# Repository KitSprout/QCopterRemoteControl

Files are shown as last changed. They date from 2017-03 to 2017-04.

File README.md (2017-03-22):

QCopterRC
========





QCopterRemoteControl 是一個遙控器開板，四軸飛行器的控制裝置，用來與 QCopterFlightControl 溝通、控制，板上搭載搖桿與感測器，並外接顯示螢幕，可以將四軸上的回傳回來的資訊顯示出來，螢幕建立了簡單的操作介面，方便使用者設定、觀察飛控板，目前遙控器有 QCopterRC 與 QCopterRCs 兩種版本，前者使用芯片效能較高、功能多，帶高解析度的螢幕，後者功能較為簡潔，製作成本比較低。目前開發著重於 QCopterRCs，想了解 QCopterRC 的可以進入該分支 [branche](https://github.com/KitSprout/QCopterRemoteControl/tree/QCopterRC)

Hardware
========
* 控制器　 : [STM32F411CE](http://www.st.com/en/microcontrollers/stm32f411ce.html) 48Pin 100MHz DSP FPU
* 顯示器　 : [OLED_1.5-inch](https://github.com/KitSprout/OLED_1.5-inch) ( SSD1351 1.5" 128*128 )，使用 SPI 操作
* 感測器　 : [MPU9250](https://www.invensense.com/products/motion-tracking/9-axis/mpu-9250/)
* 無線傳輸 : [nRF24L01P](http://www.nordicsemi.com/eng/Products/2.4GHz-RF/nRF24L01P) + PA + LNA
* 設計軟體 [Altium Designer 17](http://www.altium.com/en/products/altium-designer) ( PcbLib use AD [PcbLib v2.16](https://github.com/KitSprout/AltiumDesigner_PcbLibrary/releases/tag/v2.16) )

View
========


<br />
[more photo...](https://goo.gl/photos/wA4TmWAdz5D3ZGH7A)

Config
========


Schematic
========


Get it
========
Ruten Shop

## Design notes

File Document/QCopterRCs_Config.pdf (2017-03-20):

PORT | AF0 SYS | AF1 TIM1 TIM2 | AF2 TIM3 TIM4 TIM5 | AF3 TIM9 TIM10 TIM11 | AF4 I2C1 I2C2 I2C3 | AF5 SPI1 SPI2 SPI4 | AF6 SPI3 SPI4 SPI5 | AF7 SPI3 USART1 USART2 | AF8 USART6 | AF9 I2C2 I2C3 | AF10 OTG_FS | AF12 SDIO | ADC | 配置

PA

PB

PC

0 | CH1 / ETR | CH1 | CTS | ADC1_IN0 | X | AD_JSL1
1 | CH2 | CH2 | MOSI | RTS | ADC1_IN1 | X | AD_JSL2
2 | CH3 | CH3 | CH1 | TX | ADC1_IN2 | X | AD_BAT
3 | CH4 | CH4 | CH2 | RX | ADC1_IN3 | X | KEY_JSL
4 | NSS | NSS | CK | ADC1_IN4 | X | OLED_CS
5 | CH1 / ETR | SCK | ADC1_IN5 | X | OLED_SCK
6 | BKIN | CH1 | MISO | CMD | ADC1_IN6 | X | OLED_RES
7 | CH1N | CH2 | MOSI | ADC1_IN7 | X | OLED_SDI
8 | MCO1 | CH1 | SCL | CK | SOF | D1 | X | KEY_S2
9 | CH2 | SMBA | TX | VBUS | D2 | X | SWD_TX
10 | CH3 | MOSI | RX | ID | X | SWD_RX
11 | CH4 | MISO | CTS | TX | DM | X | KEY_S1
12 | ETR | MISO | RTS | RX | DP | X | KEY_SR
13 | SDIO | X | SWDIO
14 | SCLK | X | SWCLK
15 | JTDI | CH1 / ETR | NSS | NSS | TX | X | NRF_CSN
0 | CH2N | CH3 | SCK | ADC1_IN8 | X | AD_JSR2
1 | CH3N | CH4 | NSS | ADC1_IN9 | X | AD_JSR1
2 | BOOT | X | KEY_JSR
3 | JTDO | CH2 | SCK | SCK | RX | SDA | X | NRF_SCK
4 | JTRST | CH1 | MISO | MISO | SDA | D0 | X | NRF_SDO
5 | CH2 | SMBA | MOSI | MOSI | D3 | X | NRF_SDI
6 | CH1 | SCL | TX | X | NRF_CE
7 | CH2 | SDA | RX | D0 | X | NRF_IRQ
8 | CH3 | CH1 | SCL | MOSI | SDA | D4 | X | KEY_SP
9 | CH4 | CH1 | SDA | NSS | SDA | D5 | X | KEY_SL
10 | CH3 | SCL | SCK | D7 | X | OLED_DC
11 | CH4 | X
12 | BKIN | SMBA | NSS | NSS | SCK | X | IMU_CSM
13 | CH1N | SCK | SCK | X | IMU_SCK
14 | CH2N | MISO | D6 | X | IMU_SDO
15 | RTC | CH3N | MOSI | CK | X | IMU_SDI
13 | X | LED_B
14 | X | LED_G
15 | X | LED_R

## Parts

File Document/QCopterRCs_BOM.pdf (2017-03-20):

Comment | Description | Designator | Footprint | LibRef | Quantity | Value
MX1.25_2P | MX | BAT | MX1.25_S90_2P | MX1.25_2P | 1
Cap_0603 | Capacitor | C1, C2, C3, C4, C5, C6, C7, C8, C9, C11, C12, C13, C14, C15 | CAP_0603 | Cap_0603 | 14 | 1u, 0.1u, 0.1u, 22n, 0.1u, 0.1u, 0.1u, 0.1u, 0.1u, 10p, 10p, 10n, 0.1u, 0.1u
Cap_Tan_0805 | Capacitor | C10 | CAP_TAN_P0805 | Cap_Tan_0805 | 1 | 2.2u
LED_0603 | LED | D1 | LED_0603_YELLOW | LED_0603 | 1
LED_0805 | LED | D2 | LED_0805_RED | LED_0805 | 1
LED_0805 | LED | D3 | LED_0805_GREEN | LED_0805 | 1
LED_0805 | LED | D4 | LED_0805_BLUE | LED_0805 | 1
JoyStick | JoyStick | JSL, JSR | JoyStick | JoyStick | 2
nRF24L01P_PA_LN A | Module | NRF24 | NRF24L01P_PA_LN A | nRF24L01P_PA_LN A | 1
OLED_1.5_128*128 | Module | OLED | OLED_1.5_128x128 | OLED_1.5_128*128 | 1
SwitchSPDT_2.8x6. 6_90 | Switch | PW | SwitchSPDT_2.8X6. 6_90 | SwitchSPDT_2.8x6. 6_90 | 1
Res_0603 | Resistor | R1, R2, R3, R4, R5, R6, R7, R8, R9, R10, R11, R12, R13, R14, R15, R16, R17 | RES_0603 | Res_0603 | 17 | 1K, 10K, 10K, 680R, 680R, 680R, 4.7K, 4.7K, 10K, 10K, 4.7K, 4.7K, 10K, 10K, 10K, 10K, 10K
ButtonTACT_3x6x2 .5_180 | Button | S1, S2 | ButtonTACT_3x6x2 .5_180 | ButtonTACT_3x6x2 .5_180 | 2
ButtonPushLever_ 11*12_90 | Button | S3 | ButtonPushLever_ 11*12_90 | ButtonPushLever_ 11*12_90 | 1
HDR1x6_1.27 | Header | SWD | HDR1X6_1.27_180 HF | HDR1x6_1.27 | 1
RT9193 | Power | U1 | SOT23-5 | RT9193 | 1
STM32F411C | MCU | U2 | QFN_P0.5_48 | STM32F4x1C | 1
MPU6500 | Sensor Motion | U3 | QFN_P0.4_24 | MPU925x | 1
XTAL_2520_4P | Crystal Oscillator | XT | XT_2520_4 | XTAL_2520_4P | 1 | 16MHz

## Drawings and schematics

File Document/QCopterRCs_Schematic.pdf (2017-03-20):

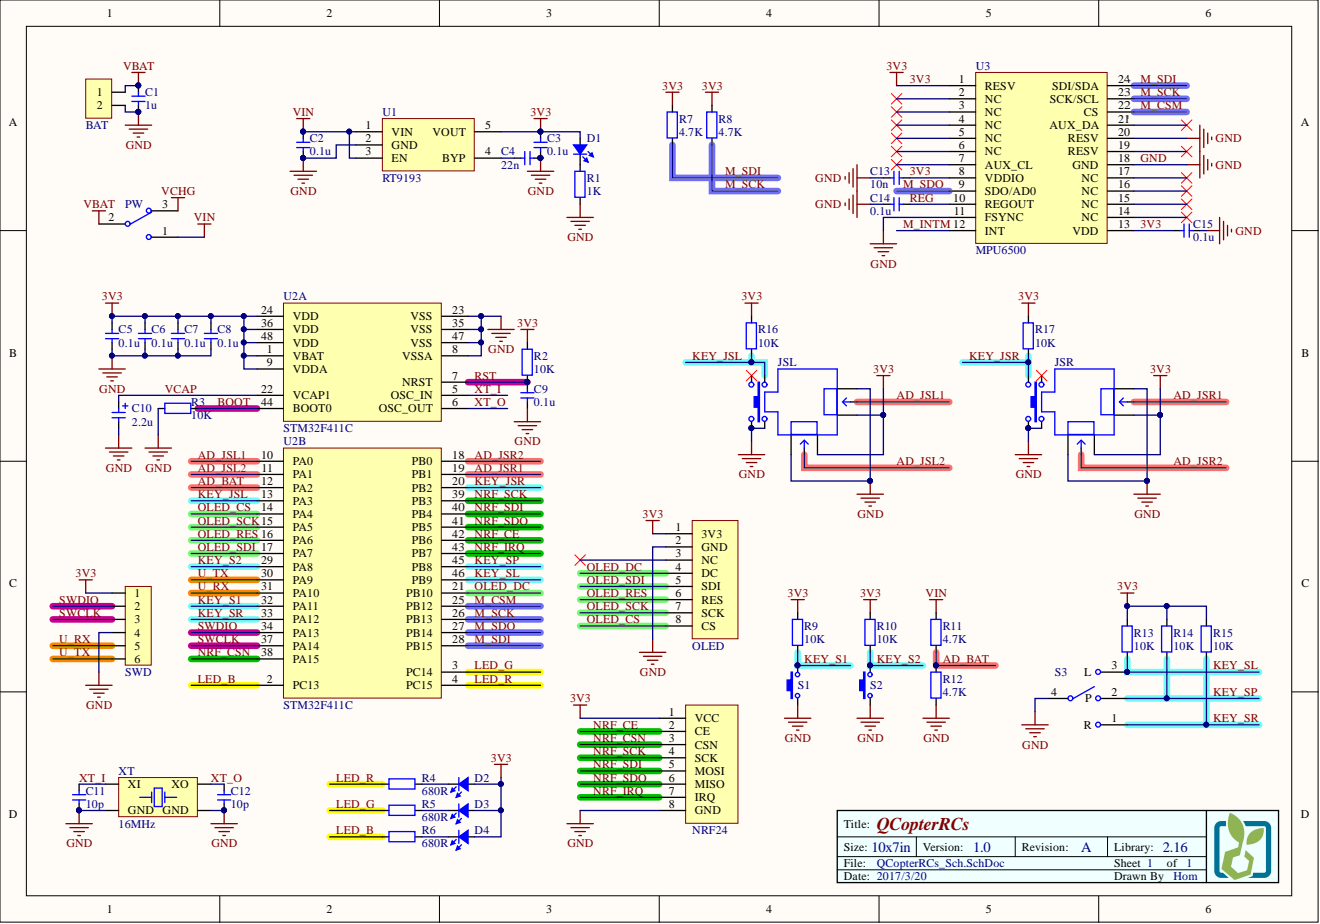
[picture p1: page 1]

GND 2
NC 3

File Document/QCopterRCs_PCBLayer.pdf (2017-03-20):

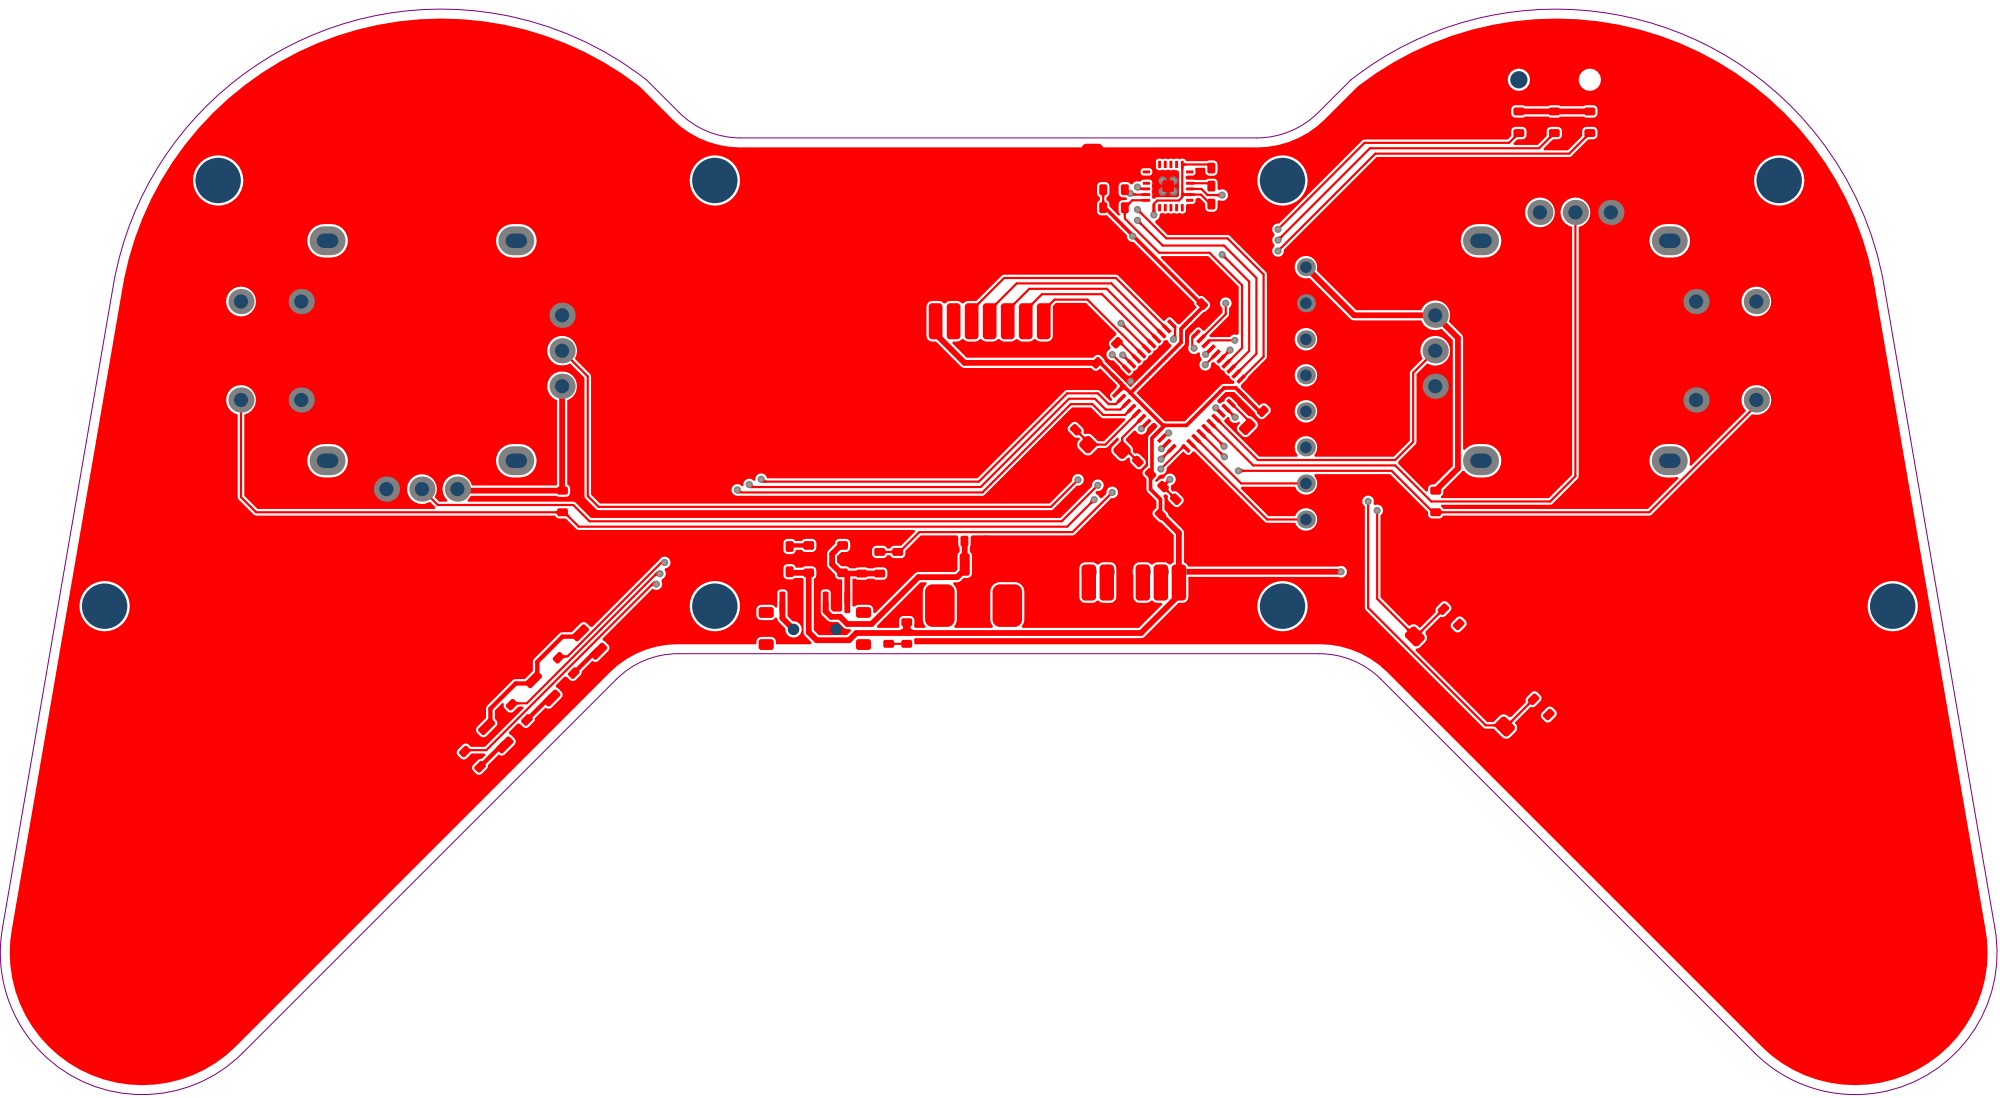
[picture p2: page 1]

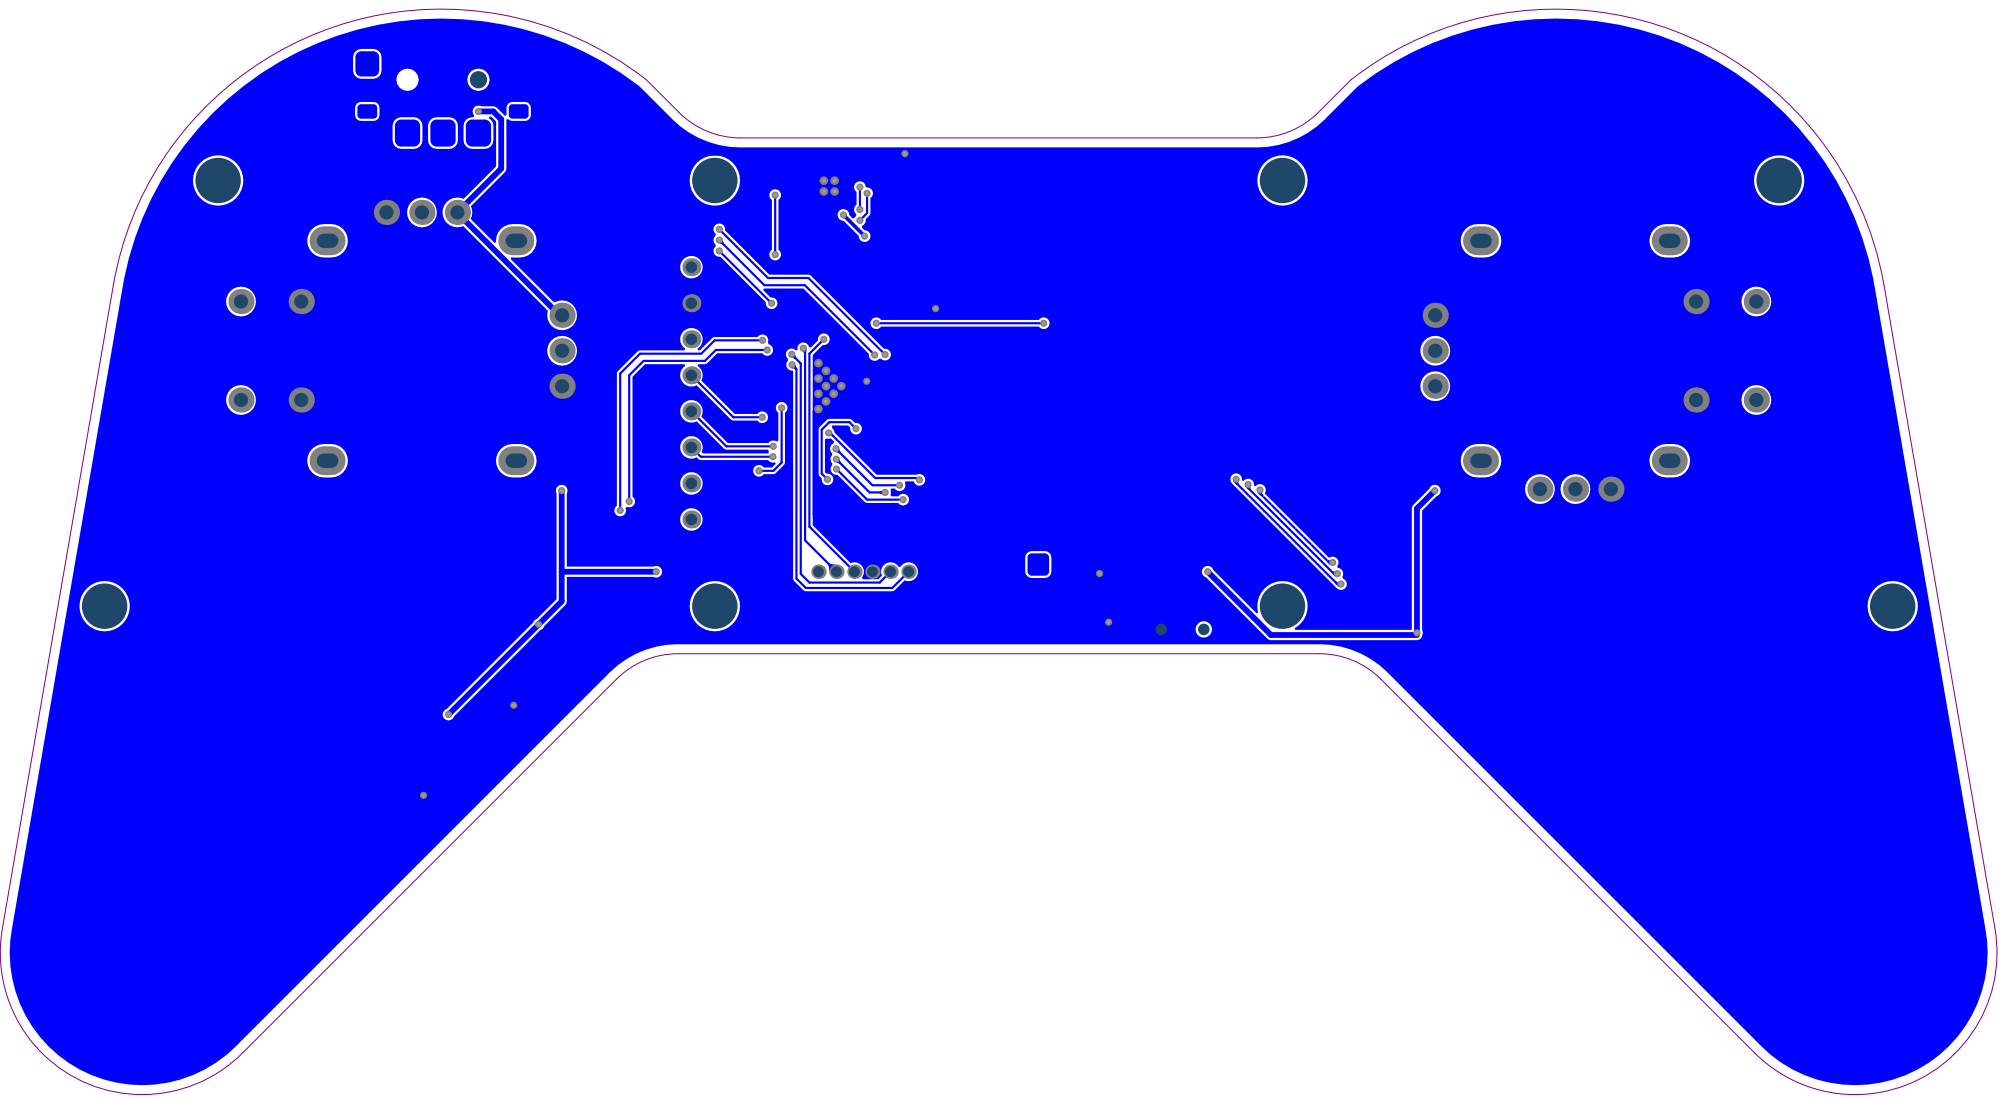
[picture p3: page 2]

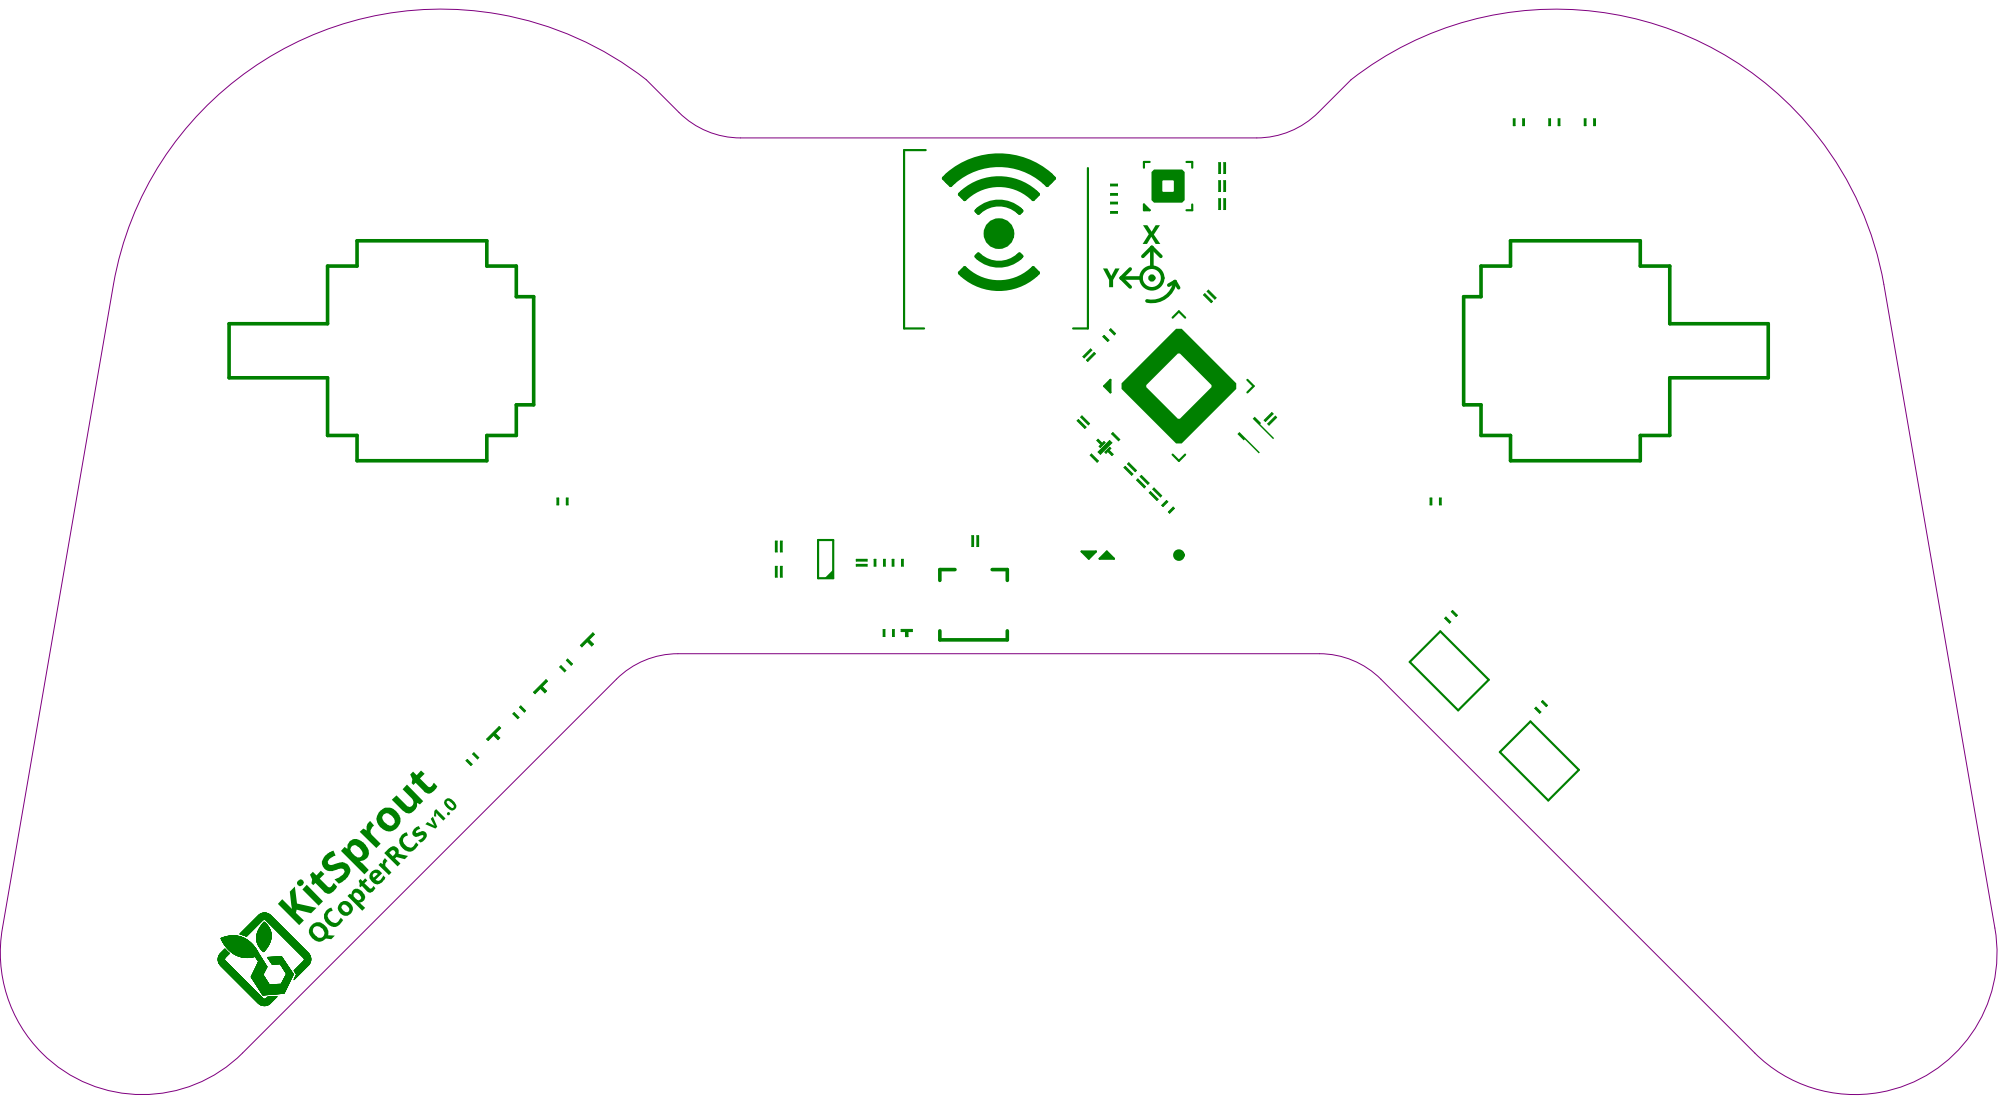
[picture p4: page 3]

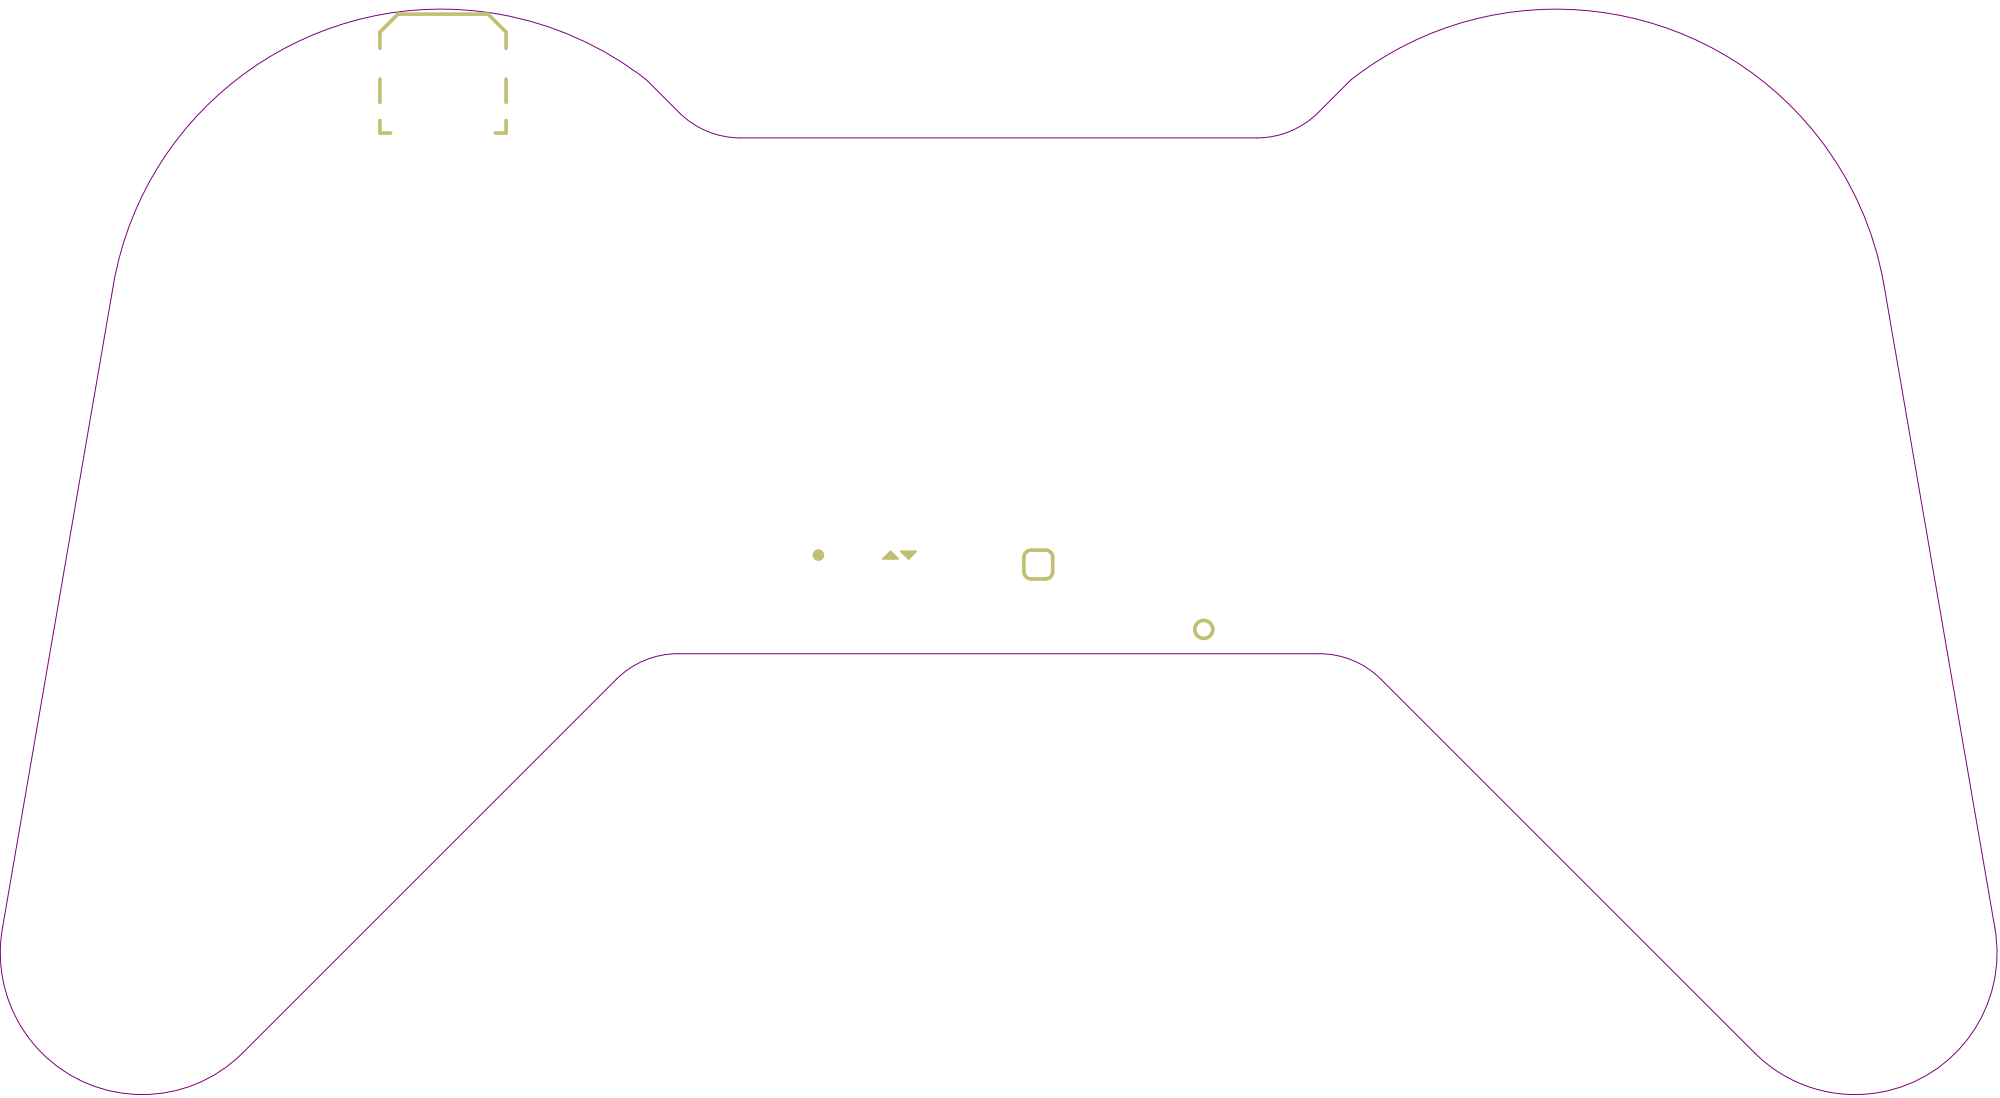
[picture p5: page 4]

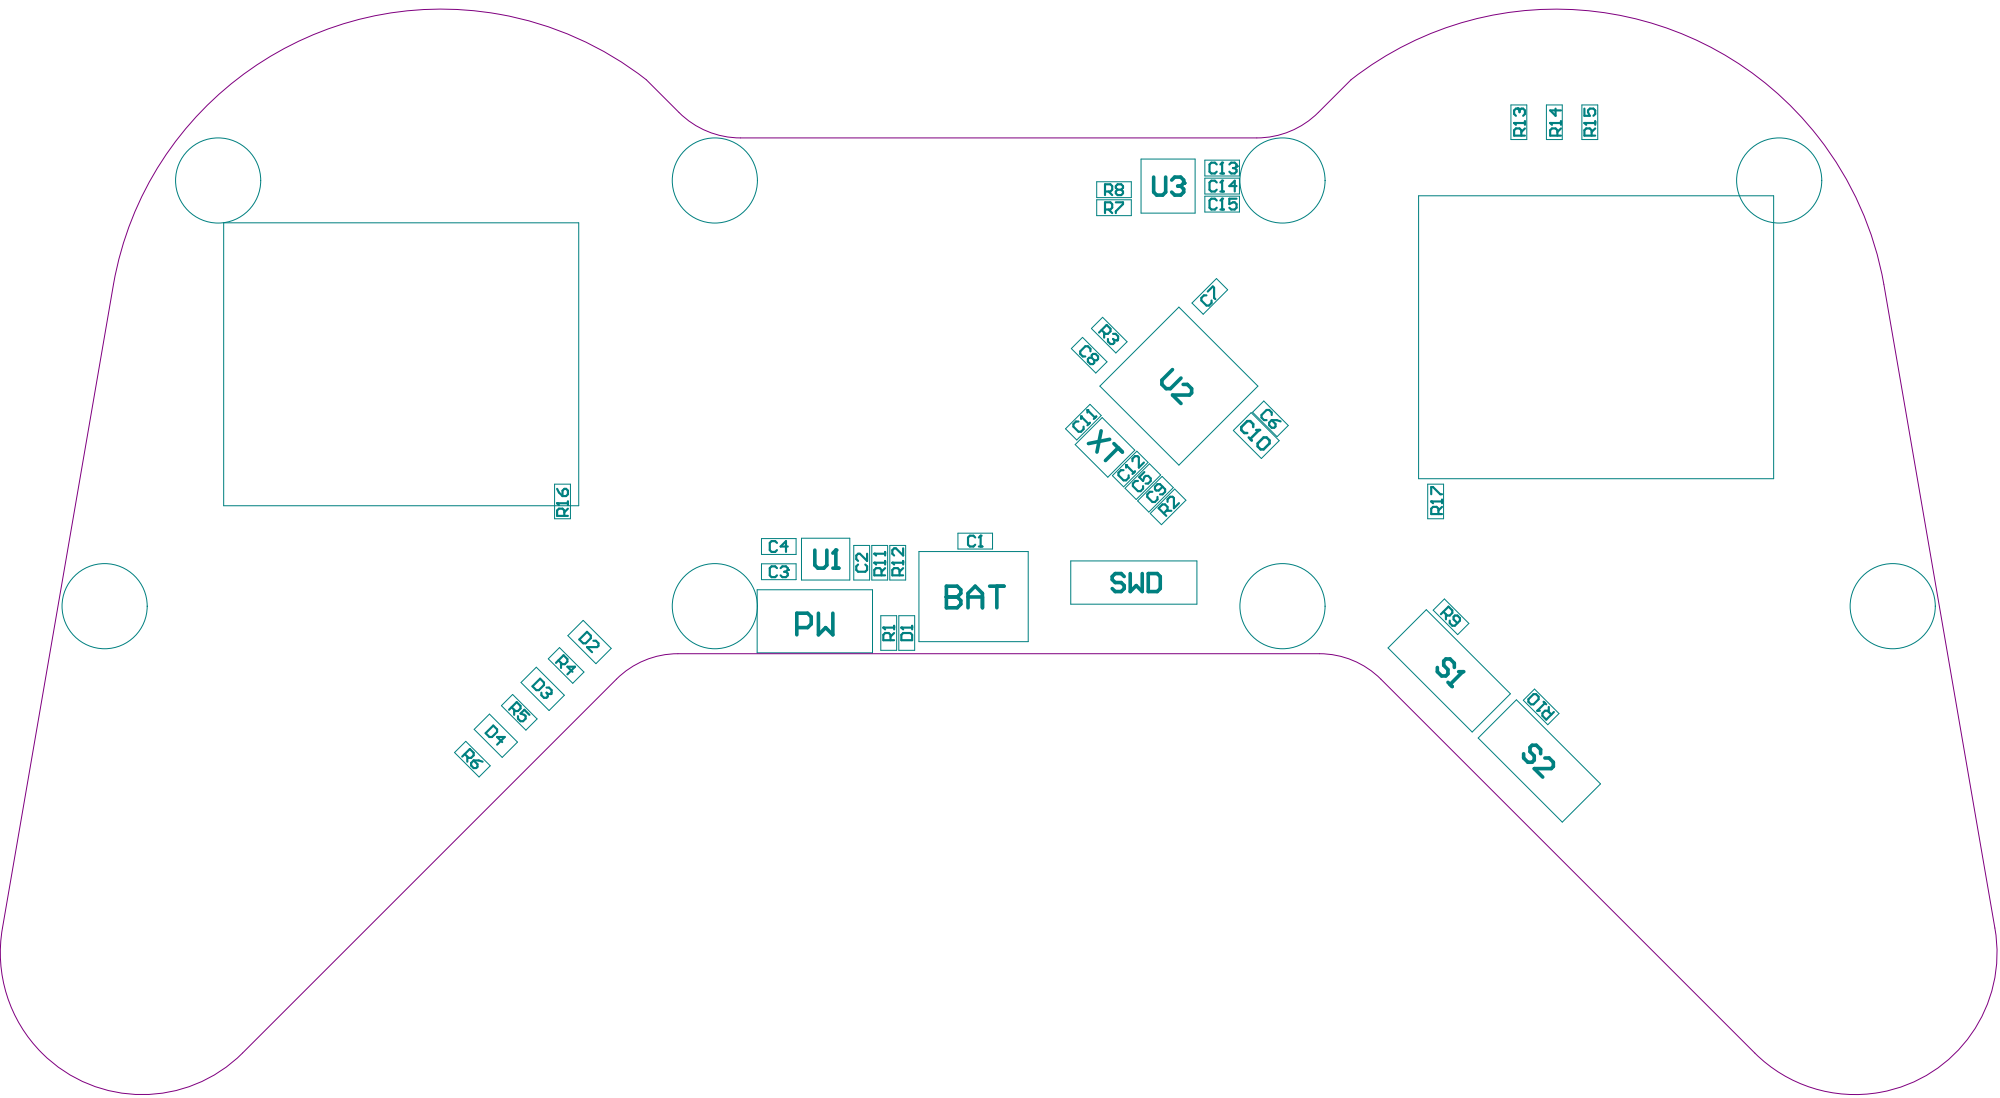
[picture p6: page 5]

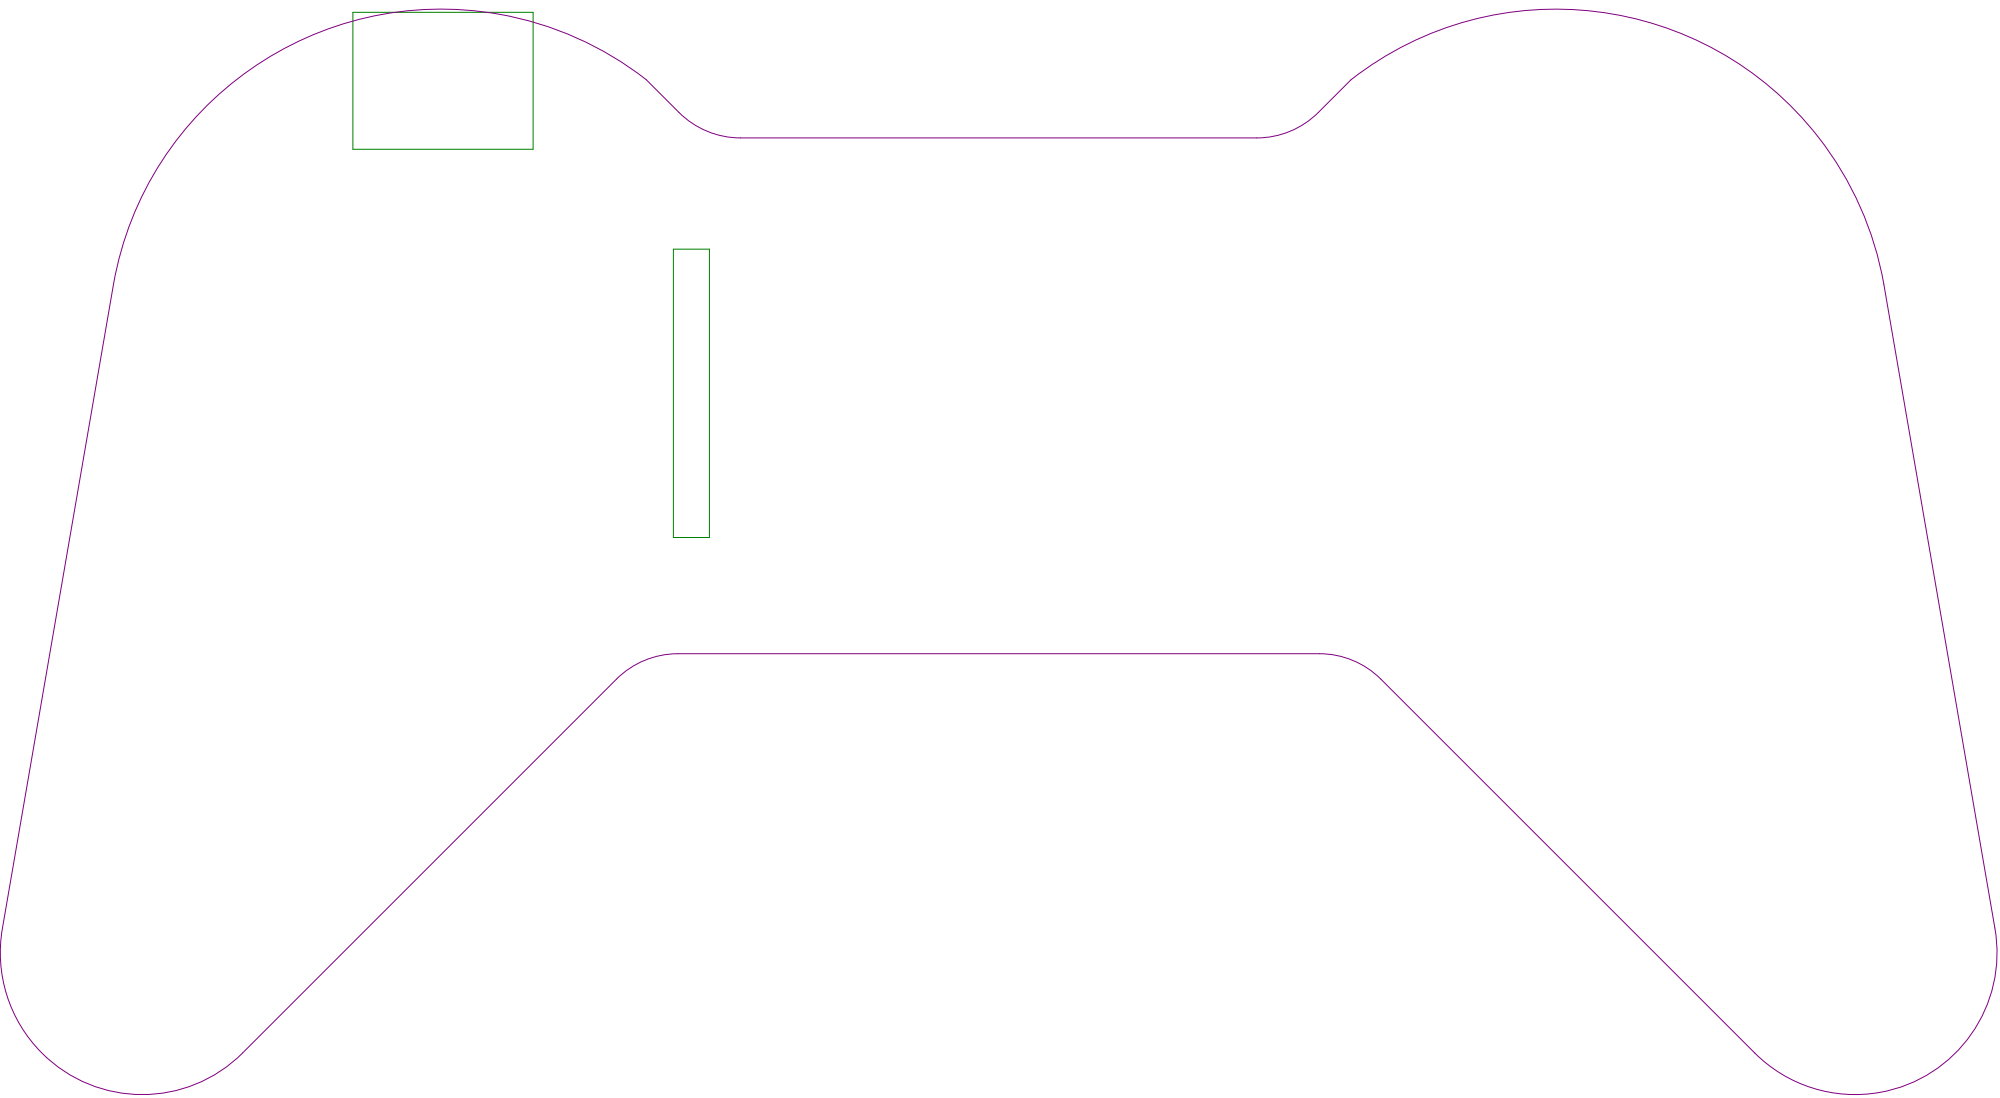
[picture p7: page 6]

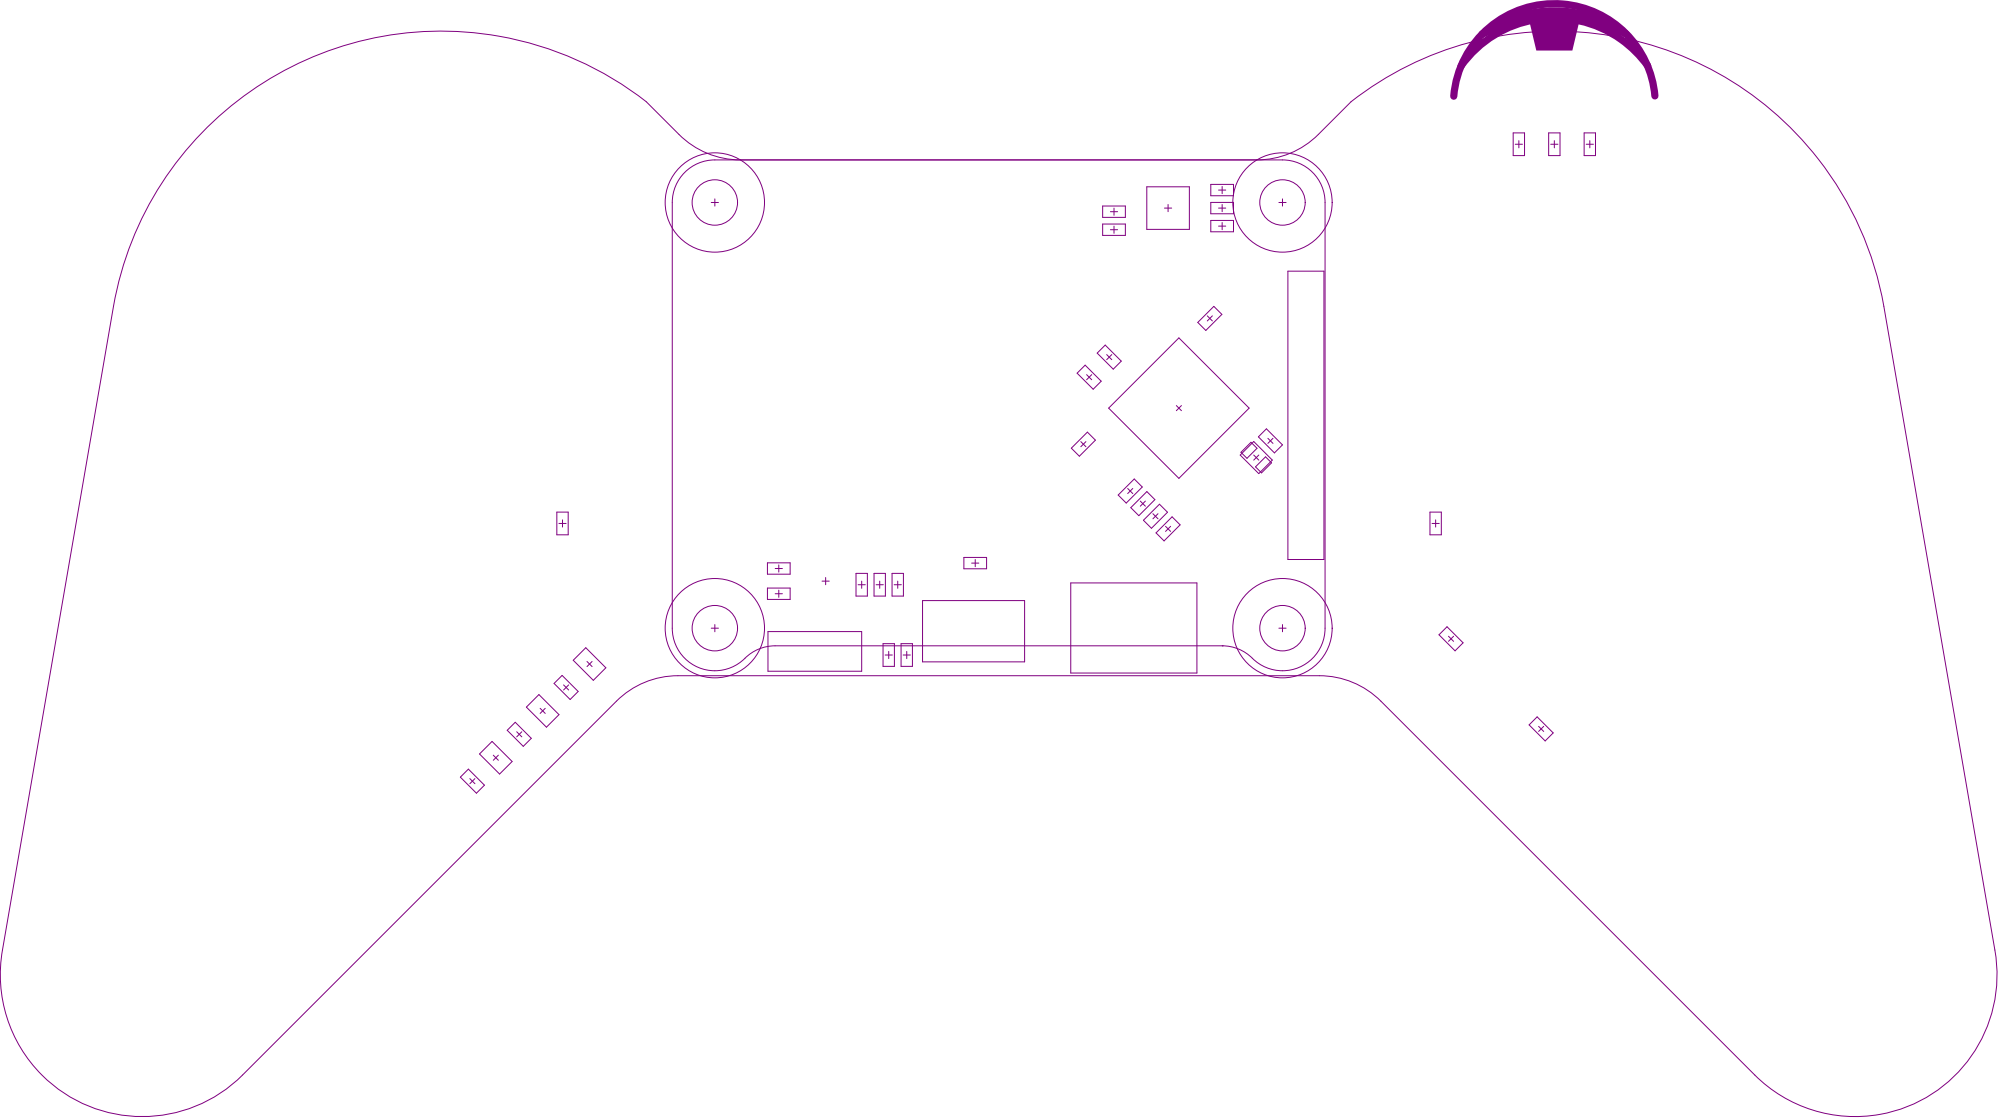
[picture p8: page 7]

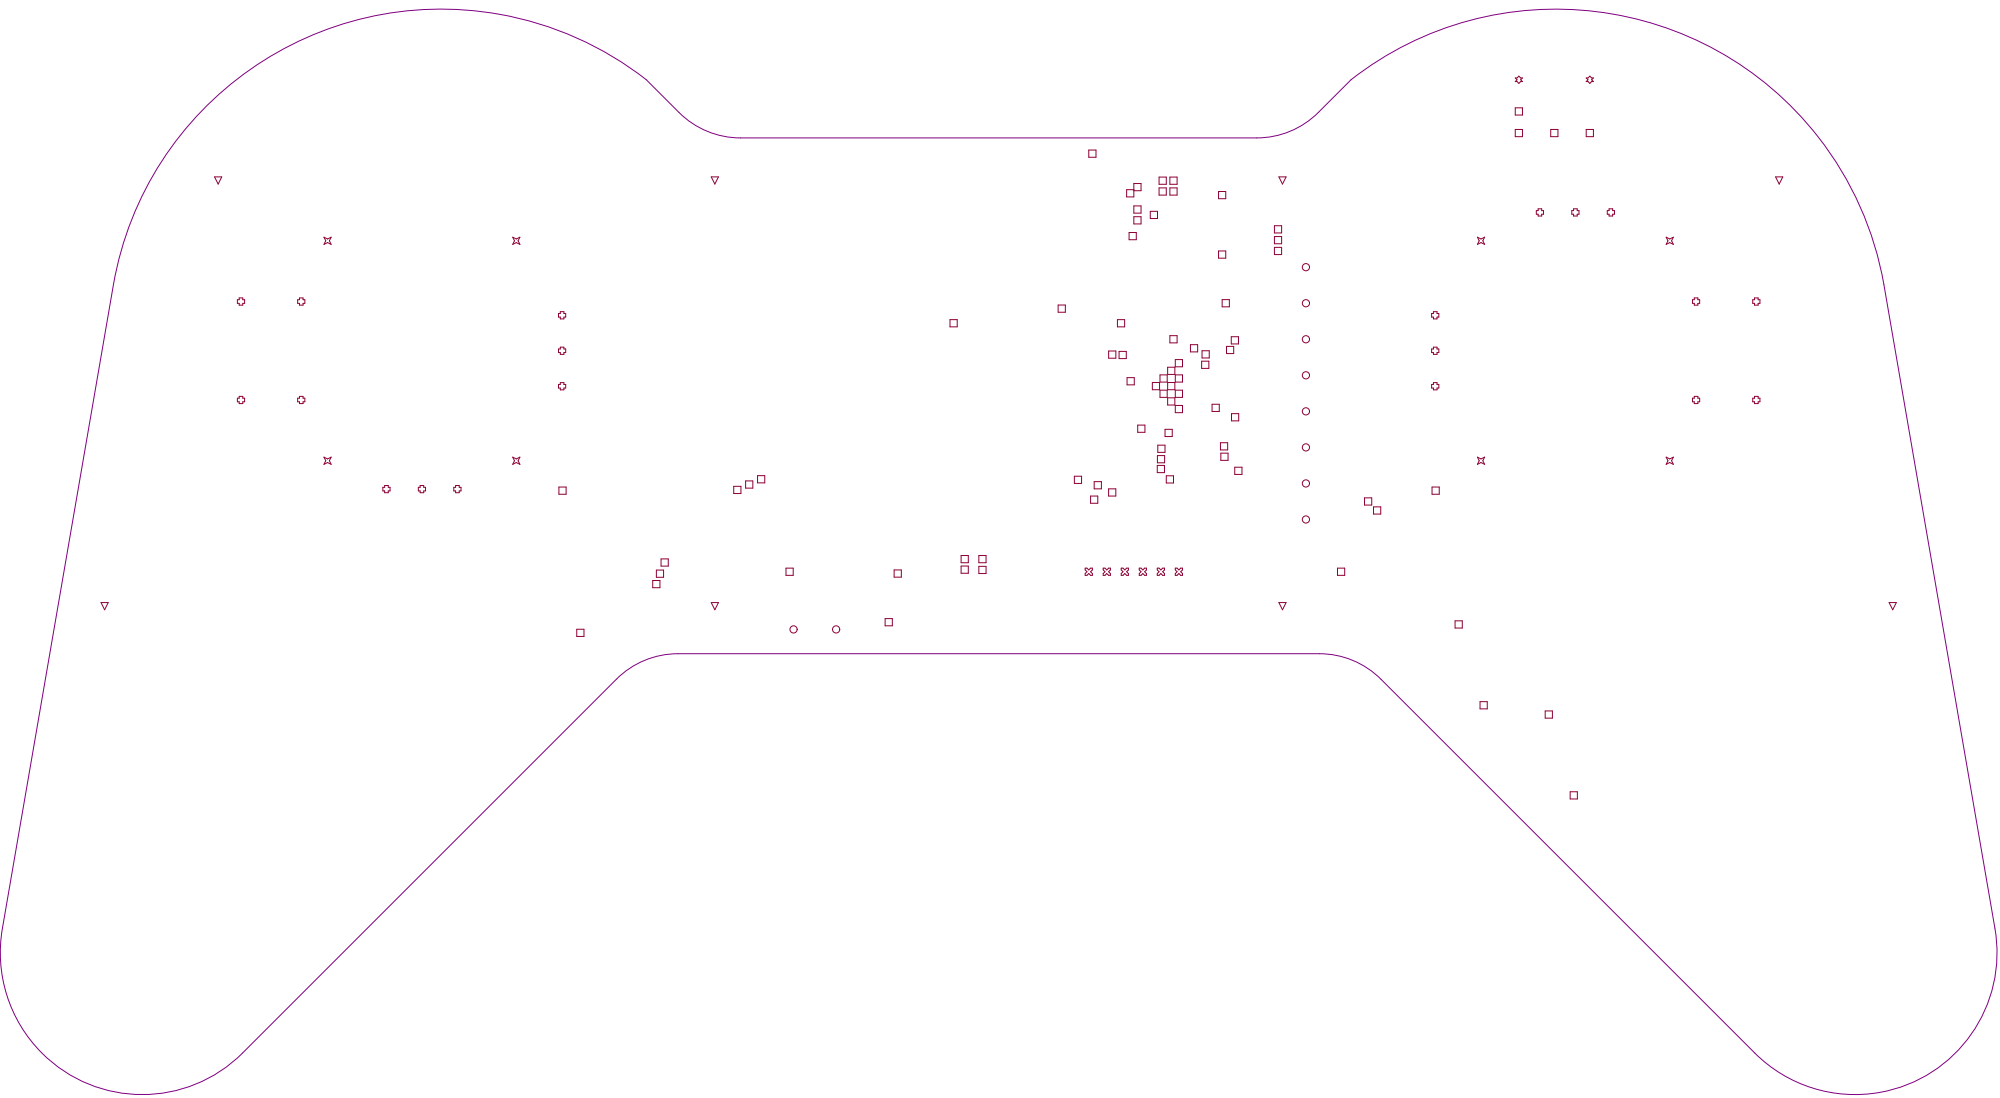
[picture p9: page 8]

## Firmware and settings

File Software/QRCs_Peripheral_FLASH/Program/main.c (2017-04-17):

/**
  *      __            ____
  *     / /__ _  __   / __/                      __  
  *    / //_/(_)/ /_ / /  ___   ____ ___  __ __ / /_ 
  *   / ,<  / // __/_\ \ / _ \ / __// _ \/ // // __/ 
  *  /_/|_|/_/ \__//___// .__//_/   \___/\_,_/ \__/  
  *                    /_/   github.com/KitSprout    
  * 
  * @file    main.c
  * @author  KitSprout
  * @date    16-Mar-2017
  * @brief   
  * 
  */

/* Includes --------------------------------------------------------------------------------*/
#include "drivers\stm32f4_system.h"
#include "drivers\stm32f4_flash.h"
#include "algorithms\compare.h"
#include "stm32f4xx_bsp.h"

/** @addtogroup STM32_Program
  * @{
  */

/* Private typedef -------------------------------------------------------------------------*/
/* Private define --------------------------------------------------------------------------*/
#define FLASH_RW_U8  1
#define FLASH_RW_U16 1
#define FLASH_RW_U32 1
#define FLASH_RW_U64 0

#define FLASH_USER_ADDR   FLASH_ADDR_SECTOR_5
#define WRITE_SECTOR      FLASH_GetSector(FLASH_USER_ADDR)

#if FLASH_RW_U8
uint8_t ReadDataU8[1024] = {0};
uint8_t WriteDataU8[1024] = {
  1,2,3,4,5,6,7,8,9,10,11,12,13,14,15,16,1,2,3,4,5,6,7,8,9,10,11,12,13,14,15,16,1,2,3,4,5,6,7,8,9,10,11,12,13,14,15,16,1,2,3,4,5,6,7,8,9,10,11,12,13,14,15,16,
  1,2,3,4,5,6,7,8,9,10,11,12,13,14,15,16,1,2,3,4,5,6,7,8,9,10,11,12,13,14,15,16,1,2,3,4,5,6,7,8,9,10,11,12,13,14,15,16,1,2,3,4,5,6,7,8,9,10,11,12,13,14,15,16,
  1,2,3,4,5,6,7,8,9,10,11,12,13,14,15,16,1,2,3,4,5,6,7,8,9,10,11,12,13,14,15,16,1,2,3,4,5,6,7,8,9,10,11,12,13,14,15,16,1,2,3,4,5,6,7,8,9,10,11,12,13,14,15,16,
  1,2,3,4,5,6,7,8,9,10,11,12,13,14,15,16,1,2,3,4,5,6,7,8,9,10,11,12,13,14,15,16,1,2,3,4,5,6,7,8,9,10,11,12,13,14,15,16,1,2,3,4,5,6,7,8,9,10,11,12,13,14,15,16,
  1,2,3,4,5,6,7,8,9,10,11,12,13,14,15,16,1,2,3,4,5,6,7,8,9,10,11,12,13,14,15,16,1,2,3,4,5,6,7,8,9,10,11,12,13,14,15,16,1,2,3,4,5,6,7,8,9,10,11,12,13,14,15,16,
  1,2,3,4,5,6,7,8,9,10,11,12,13,14,15,16,1,2,3,4,5,6,7,8,9,10,11,12,13,14,15,16,1,2,3,4,5,6,7,8,9,10,11,12,13,14,15,16,1,2,3,4,5,6,7,8,9,10,11,12,13,14,15,16,
  1,2,3,4,5,6,7,8,9,10,11,12,13,14,15,16,1,2,3,4,5,6,7,8,9,10,11,12,13,14,15,16,1,2,3,4,5,6,7,8,9,10,11,12,13,14,15,16,1,2,3,4,5,6,7,8,9,10,11,12,13,14,15,16,
  1,2,3,4,5,6,7,8,9,10,11,12,13,14,15,16,1,2,3,4,5,6,7,8,9,10,11,12,13,14,15,16,1,2,3,4,5,6,7,8,9,10,11,12,13,14,15,16,1,2,3,4,5,6,7,8,9,10,11,12,13,14,15,16,
  1,2,3,4,5,6,7,8,9,10,11,12,13,14,15,16,1,2,3,4,5,6,7,8,9,10,11,12,13,14,15,16,1,2,3,4,5,6,7,8,9,10,11,12,13,14,15,16,1,2,3,4,5,6,7,8,9,10,11,12,13,14,15,16,
  1,2,3,4,5,6,7,8,9,10,11,12,13,14,15,16,1,2,3,4,5,6,7,8,9,10,11,12,13,14,15,16,1,2,3,4,5,6,7,8,9,10,11,12,13,14,15,16,1,2,3,4,5,6,7,8,9,10,11,12,13,14,15,16,
  1,2,3,4,5,6,7,8,9,10,11,12,13,14,15,16,1,2,3,4,5,6,7,8,9,10,11,12,13,14,15,16,1,2,3,4,5,6,7,8,9,10,11,12,13,14,15,16,1,2,3,4,5,6,7,8,9,10,11,12,13,14,15,16,
  1,2,3,4,5,6,7,8,9,10,11,12,13,14,15,16,1,2,3,4,5,6,7,8,9,10,11,12,13,14,15,16,1,2,3,4,5,6,7,8,9,10,11,12,13,14,15,16,1,2,3,4,5,6,7,8,9,10,11,12,13,14,15,16,
  1,2,3,4,5,6,7,8,9,10,11,12,13,14,15,16,1,2,3,4,5,6,7,8,9,10,11,12,13,14,15,16,1,2,3,4,5,6,7,8,9,10,11,12,13,14,15,16,1,2,3,4,5,6,7,8,9,10,11,12,13,14,15,16,
  1,2,3,4,5,6,7,8,9,10,11,12,13,14,15,16,1,2,3,4,5,6,7,8,9,10,11,12,13,14,15,16,1,2,3,4,5,6,7,8,9,10,11,12,13,14,15,16,1,2,3,4,5,6,7,8,9,10,11,12,13,14,15,16,
  1,2,3,4,5,6,7,8,9,10,11,12,13,14,15,16,1,2,3,4,5,6,7,8,9,10,11,12,13,14,15,16,1,2,3,4,5,6,7,8,9,10,11,12,13,14,15,16,1,2,3,4,5,6,7,8,9,10,11,12,13,14,15,16,
  1,2,3,4,5,6,7,8,9,10,11,12,13,14,15,16,1,2,3,4,5,6,7,8,9,10,11,12,13,14,15,16,1,2,3,4,5,6,7,8,9,10,11,12,13,14,15,16,1,2,3,4,5,6,7,8,9,10,11,12,13,14,15,16
};
#endif

#if FLASH_RW_U16
uint16_t ReadDataU16[512] = {0};
uint16_t WriteDataU16[512] = {
  1,2,3,4,5,6,7,8,9,10,11,12,13,14,15,16,1,2,3,4,5,6,7,8,9,10,11,12,13,14,15,16,1,2,3,4,5,6,7,8,9,10,11,12,13,14,15,16,1,2,3,4,5,6,7,8,9,10,11,12,13,14,15,16,
  1,2,3,4,5,6,7,8,9,10,11,12,13,14,15,16,1,2,3,4,5,6,7,8,9,10,11,12,13,14,15,16,1,2,3,4,5,6,7,8,9,10,11,12,13,14,15,16,1,2,3,4,5,6,7,8,9,10,11,12,13,14,15,16,
  1,2,3,4,5,6,7,8,9,10,11,12,13,14,15,16,1,2,3,4,5,6,7,8,9,10,11,12,13,14,15,16,1,2,3,4,5,6,7,8,9,10,11,12,13,14,15,16,1,2,3,4,5,6,7,8,9,10,11,12,13,14,15,16,
  1,2,3,4,5,6,7,8,9,10,11,12,13,14,15,16,1,2,3,4,5,6,7,8,9,10,11,12,13,14,15,16,1,2,3,4,5,6,7,8,9,10,11,12,13,14,15,16,1,2,3,4,5,6,7,8,9,10,11,12,13,14,15,16,
  1,2,3,4,5,6,7,8,9,10,11,12,13,14,15,16,1,2,3,4,5,6,7,8,9,10,11,12,13,14,15,16,1,2,3,4,5,6,7,8,9,10,11,12,13,14,15,16,1,2,3,4,5,6,7,8,9,10,11,12,13,14,15,16,
  1,2,3,4,5,6,7,8,9,10,11,12,13,14,15,16,1,2,3,4,5,6,7,8,9,10,11,12,13,14,15,16,1,2,3,4,5,6,7,8,9,10,11,12,13,14,15,16,1,2,3,4,5,6,7,8,9,10,11,12,13,14,15,16,
  1,2,3,4,5,6,7,8,9,10,11,12,13,14,15,16,1,2,3,4,5,6,7,8,9,10,11,12,13,14,15,16,1,2,3,4,5,6,7,8,9,10,11,12,13,14,15,16,1,2,3,4,5,6,7,8,9,10,11,12,13,14,15,16,
  1,2,3,4,5,6,7,8,9,10,11,12,13,14,15,16,1,2,3,4,5,6,7,8,9,10,11,12,13,14,15,16,1,2,3,4,5,6,7,8,9,10,11,12,13,14,15,16,1,2,3,4,5,6,7,8,9,10,11,12,13,14,15,16
};
#endif

#if FLASH_RW_U32
uint32_t ReadDataU32[256] = {0};
uint32_t WriteDataU32[256] = {
  1,2,3,4,5,6,7,8,9,10,11,12,13,14,15,16,1,2,3,4,5,6,7,8,9,10,11,12,13,14,15,16,1,2,3,4,5,6,7,8,9,10,11,12,13,14,15,16,1,2,3,4,5,6,7,8,9,10,11,12,13,14,15,16,
  1,2,3,4,5,6,7,8,9,10,11,12,13,14,15,16,1,2,3,4,5,6,7,8,9,10,11,12,13,14,15,16,1,2,3,4,5,6,7,8,9,10,11,12,13,14,15,16,1,2,3,4,5,6,7,8,9,10,11,12,13,14,15,16,
  1,2,3,4,5,6,7,8,9,10,11,12,13,14,15,16,1,2,3,4,5,6,7,8,9,10,11,12,13,14,15,16,1,2,3,4,5,6,7,8,9,10,11,12,13,14,15,16,1,2,3,4,5,6,7,8,9,10,11,12,13,14,15,16,
  1,2,3,4,5,6,7,8,9,10,11,12,13,14,15,16,1,2,3,4,5,6,7,8,9,10,11,12,13,14,15,16,1,2,3,4,5,6,7,8,9,10,11,12,13,14,15,16,1,2,3,4,5,6,7,8,9,10,11,12,13,14,15,16
};
#endif

#if FLASH_RW_U64
uint64_t ReadDataU64[128] = {0};
uint64_t WriteDataU64[128] = {
  1,2,3,4,5,6,7,8,9,10,11,12,13,14,15,16,1,2,3,4,5,6,7,8,9,10,11,12,13,14,15,16,1,2,3,4,5,6,7,8,9,10,11,12,13,14,15,16,1,2,3,4,5,6,7,8,9,10,11,12,13,14,15,16,
  1,2,3,4,5,6,7,8,9,10,11,12,13,14,15,16,1,2,3,4,5,6,7,8,9,10,11,12,13,14,15,16,1,2,3,4,5,6,7,8,9,10,11,12,13,14,15,16,1,2,3,4,5,6,7,8,9,10,11,12,13,14,15,16
};
#endif

/* Private macro ---------------------------------------------------------------------------*/
/* Private variables -----------------------------------------------------------------------*/
/* Private function prototypes -------------------------------------------------------------*/
/* Private functions -----------------------------------------------------------------------*/

void testFlash( void )
{
  LED_R_Set();
  LED_G_Set();
  LED_B_Set();

#if FLASH_RW_U8
  FLASH_EraseSectors(WRITE_SECTOR, 1);
  FLASH_WritePageU8(FLASH_USER_ADDR, WriteDataU8, 1024);
  FLASH_ReadPageU8(FLASH_USER_ADDR, ReadDataU8, 1024);
  if (CMP_ArrayU8(WriteDataU8, ReadDataU8, 1024) == HAL_OK)
    LED_R_Reset();
  delay_ms(500);
#endif

#if FLASH_RW_U16
  FLASH_EraseSectors(WRITE_SECTOR, 1);
  FLASH_WritePageU16(FLASH_USER_ADDR, WriteDataU16, 512);
  FLASH_ReadPageU16(FLASH_USER_ADDR, ReadDataU16, 512);
  if (CMP_ArrayU16(WriteDataU16, ReadDataU16, 512) == HAL_OK)
    LED_G_Reset();
  delay_ms(500);
#endif

#if FLASH_RW_U32
  FLASH_EraseSectors(WRITE_SECTOR, 1);
  FLASH_WritePageU32(FLASH_USER_ADDR, WriteDataU32, 256);
  FLASH_ReadPageU32(FLASH_USER_ADDR, ReadDataU32, 256);
  if (CMP_ArrayU32(WriteDataU32, ReadDataU32, 256) == HAL_OK)
    LED_B_Reset();
  delay_ms(500);
#endif

#if FLASH_RW_U64
  FLASH_EraseSectors(WRITE_SECTOR, 1);
  FLASH_WritePageU64(FLASH_USER_ADDR, WriteDataU64, 128);
  FLASH_ReadPageU64(FLASH_USER_ADDR, ReadDataU64, 128);
  if (CMP_ArrayU64(WriteDataU64, ReadDataU64, 128) == HAL_OK) {
    LED_R_Toggle();
    delay_ms(100);
    LED_R_Toggle();
    delay_ms(100);
  }
  delay_ms(500);
#endif

  delay_ms(1000);
}

int main( void )
{
  HAL_Init();
  BSP_GPIO_Config();

  testFlash();

  while (1) {
    LED_R_Toggle();
    LED_G_Toggle();
    LED_B_Toggle();
    delay_ms(200);
  }
}

/*************************************** END OF FILE ****************************************/

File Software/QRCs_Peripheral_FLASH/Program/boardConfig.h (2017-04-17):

/**
  *      __            ____
  *     / /__ _  __   / __/                      __  
  *    / //_/(_)/ /_ / /  ___   ____ ___  __ __ / /_ 
  *   / ,<  / // __/_\ \ / _ \ / __// _ \/ // // __/ 
  *  /_/|_|/_/ \__//___// .__//_/   \___/\_,_/ \__/  
  *                    /_/   github.com/KitSprout    
  * 
  * @file    boardConfig.h
  * @author  KitSprout
  * @date    16-Mar-2017
  * @brief   
  * 
  */

/* Define to prevent recursive inclusion ---------------------------------------------------*/
#ifndef __BOARDCONFIG_H
#define __BOARDCONFIG_H

#ifdef __cplusplus
 extern "C" {
#endif

/* Includes --------------------------------------------------------------------------------*/
/* Exported types --------------------------------------------------------------------------*/
/* Exported constants ----------------------------------------------------------------------*/

#define KS_HW_BOARD_NAME              "QCopterRCs"
#define KS_HW_MCU_NAME                "STM32F411CE"

#define KS_HW_CLOCK_SOUCE_HSE
//#define KS_HW_USE_CLOCK_SOUCE_HSI


/* -------- LED and KEY */
   
#define LED_R_PIN                     GPIO_PIN_15
#define LED_R_GPIO_PORT               GPIOC
#define LED_R_Set()                   __GPIO_SET(LED_R_GPIO_PORT, LED_R_PIN)
#define LED_R_Reset()                 __GPIO_RST(LED_R_GPIO_PORT, LED_R_PIN)
#define LED_R_Toggle()                __GPIO_TOG(LED_R_GPIO_PORT, LED_R_PIN)

#define LED_G_PIN                     GPIO_PIN_14
#define LED_G_GPIO_PORT               GPIOC
#define LED_G_Set()                   __GPIO_SET(LED_G_GPIO_PORT, LED_G_PIN)
#define LED_G_Reset()                 __GPIO_RST(LED_G_GPIO_PORT, LED_G_PIN)
#define LED_G_Toggle()                __GPIO_TOG(LED_G_GPIO_PORT, LED_G_PIN)

#define LED_B_PIN                     GPIO_PIN_13
#define LED_B_GPIO_PORT               GPIOC
#define LED_B_Set()                   __GPIO_SET(LED_B_GPIO_PORT, LED_B_PIN)
#define LED_B_Reset()                 __GPIO_RST(LED_B_GPIO_PORT, LED_B_PIN)
#define LED_B_Toggle()                __GPIO_TOG(LED_B_GPIO_PORT, LED_B_PIN)

#define KEY_S1_PIN                    GPIO_PIN_11
#define KEY_S1_GPIO_PORT              GPIOA
#define KEY_S1_Read()                 (__GPIO_READ(KEY_S1_GPIO_PORT, KEY_S1_PIN) != KEY_S1_PIN)

#define KEY_S2_PIN                    GPIO_PIN_8
#define KEY_S2_GPIO_PORT              GPIOA
#define KEY_S2_Read()                 (__GPIO_READ(KEY_S2_GPIO_PORT, KEY_S2_PIN) != KEY_S2_PIN)

#define KEY_PL_PIN                    GPIO_PIN_9
#define KEY_PL_GPIO_PORT              GPIOB
#define KEY_PL_Read()                 (__GPIO_READ(KEY_PL_GPIO_PORT, KEY_PL_PIN) != KEY_PL_PIN)

#define KEY_PP_PIN                    GPIO_PIN_8
#define KEY_PP_GPIO_PORT              GPIOB
#define KEY_PP_Read()                 (__GPIO_READ(KEY_PP_GPIO_PORT, KEY_PP_PIN) != KEY_PP_PIN)

#define KEY_PR_PIN                    GPIO_PIN_12
#define KEY_PR_GPIO_PORT              GPIOA
#define KEY_PR_Read()                 (__GPIO_READ(KEY_PR_GPIO_PORT, KEY_PR_PIN) != KEY_PR_PIN)

#define KEY_JR_PIN                    GPIO_PIN_2
#define KEY_JR_GPIO_PORT              GPIOB
#define KEY_JR_Read()                 (__GPIO_READ(KEY_JR_GPIO_PORT, KEY_JR_PIN) != KEY_JR_PIN)

#define KEY_JL_PIN                    GPIO_PIN_3
#define KEY_JL_GPIO_PORT              GPIOA
#define KEY_JL_Read()                 (__GPIO_READ(KEY_JL_GPIO_PORT, KEY_JL_PIN) != KEY_JL_PIN)

/* Exported functions ----------------------------------------------------------------------*/

#ifdef __cplusplus
}
#endif

#endif

/*************************************** END OF FILE ****************************************/

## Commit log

2013-11-16 Update QCopterRC Mini
    [QCopterRC.PrjPCB, QCopterRC_ETH_Sch.SchDoc, QCopterRC_EXTERN_Sch.SchDoc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]
2013-11-30 Update QCopterRC v0.0 11/30
    [QCopterRC.PrjPCB, QCopterRC_CAMSPI_Sch.SchDoc, QCopterRC_ETH_Sch.SchDoc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]
2013-12-05 Update QCopterRC v0.0 12/05
    [QCopterRC_CAMSPI_Sch.SchDoc, QCopterRC_LCD_Sch.SchDoc, QCopterRC_MAIN_Sch.SchDoc]
2013-12-17 Update QCopterRC v1.0 12/17
    更新 QCopterRC 版本 v1.0 電路
    [QCopterRC.PrjPCB, QCopterRC_MAIN_Sch.SchDoc]
2013-12-21 Update Readme and Test Program 12/21
    更新 Readme
    新增測試程式
    . TestLED
    . TestUART
    . TestSDIO
    . TestFSMC
2013-12-21 Update TEST_QCopterRC_FFCSPI-TFT2.2 12/21
    新增 FFCSPI - TFT2.2 測試程式
2013-12-21 Update QCopterRC v1.1
    更新 QCopterRC 電路版本 v1.1
    修正內容：
    . IMU 和 EXT 部分 SDA SCL 接反問題
    . 按鍵標示錯誤，KEY_Rx 與 KEY_Lx 接反
    . 修改 PA0 與 PB2 按鍵位置，改至 KEY_Sx
    [QCopterRC.PrjPCB, QCopterRC_CAMSPI_Sch.SchDoc, QCopterRC_EXTERN_Sch.SchDoc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]
2013-12-21 Update Readme 12/21
    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
2013-12-21 Update TestProgram - FSMC & FFCSPI 12/22
    更新測試程式 FSMC 和 FFCSPI
    加入 Logo 圖片顯示
2013-12-22 Update TestADC Program 12/22
    新增 ADC 測試程式
2013-12-22 Update QCopterRC_WaveForm 12/23
    新增簡易示波器程式
2013-12-22 Update Readme 12/23
    更新 Readme 內容
2013-12-23 Update TEST_QCopterRC_NRF 12/23
    新增 nRF24L01 測試程式
2013-12-23 Update Readme 12/24
    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
2013-12-24 Update QCopterRC_RemoteControl 12/25
    新增遙控程式，目前無遙控功能，正在完善中 ...
2013-12-25 Update Readme 12/26
    增加 QFC TO QRC 的傳輸資料格式
2013-12-26 Add TEST_QCopterRC_KeyBoard 12/26
    新增遙控器鍵盤 ( 按鍵+搖桿 ) 測試程式
2013-12-26 Update QCopterRC_RemoteControl 12/26
    1. 微調介面
    2. 加入示波器功能、鍵盤測試功能
    3. 加入與 QFC 的傳輸格式 ( 目前完成 QFC to QRC 的部分 )
2013-12-28 Add TEST_QCopterRC_FLASH 12/29
    新增 FLASH 範例
2014-01-01 Update TEST_QCopterRC_LED 01/01
    ．修改 LED 範例內容
    ．新增 Readme.md
2014-01-01 Update TEST_QCopterRC_SDIO 01/01
    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
2014-01-04 Update QCopterRC_RemoteControl 01/04
    更新遙控程式
    ．完善 QRC to QFC 傳輸
    ．微調部分介面
2014-01-04 Update Readme.md 01/04
    新增 QRC TO QFC 傳輸格式示意圖
2014-01-05 Update QCopterRC_RemoteControl 01/05
    ．加入油門顯示
    ．改善傳輸可能出現的 BUG
    ．螢幕 PutNum 函式加入字型選擇 ( 原本預設 1608 字型 )
    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
2014-01-05 Add QCopterRC_Bitmap 01/06
    新增 Bitmap 檔案讀取
2014-01-05 Update QCopterRC_RemoteControl 01/06
    微調油門介面
2014-01-05 Update Readme.md 01/06
    修正圖片比例
2014-01-06 Update QCopterRC_RemoteControl 01/06
    ．將眾多測試功能移至選單 TEST 上，透過按鍵切換
    ．新增 3D 旋轉功能、字型、顏色(尚未完善)
2014-01-06 Updtae QCopterRC_RemoteControl 01/06
    ．新增簡單 3D 處理函數，並實際 DEMO
2014-01-06 Update Readme.md 01/07
    新增相片
2014-01-07 Update Readme.md 01/09
    新增預計 QCopterRC v2.0 版本預計更新內容
2014-01-08 Add TEST_QCopterRC_IMU 01/09
    新增 IMU 測試程式，尚未實際燒錄測試過
2014-01-09 Update Readme.md 01/09
    修改 IMU 6-DOF 連結
2014-01-09 Update Readme.md 01/09
    更新 PCB LIB 連結
2014-01-14 Update Readme.md 01/14
    轉移至 QCopter
2014-01-20 Update Readme.md 01/20
    詳細授權部分
2014-01-20 Add LICENSE 01/20
    加入授權聲明
2014-01-20 Change Directory 01/20
    Program 資料夾改名為 Software
2014-01-20 Update Readme.md 01/20
    修改連結
2014-03-18 Add TEST_QCopterRC_FFCSPI-MPU9250 03/18
    新增 FFCSPI-MPU9250 測試程式
2014-04-01 Update TEST_QCopterRC_FFCSPI-MPU9250 04/02
    加入示波器顯示數據
2015-04-02 Update README 04/03
    修改預計更新內容
2017-03-20 Add QRCs Hardware v1.0 03/20
    [QCopterRC.PrjPCB, QCopterRC_ETH_Sch.SchDoc, QCopterRC_EXTERN_Sch.SchDoc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]

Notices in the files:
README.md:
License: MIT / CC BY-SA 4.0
